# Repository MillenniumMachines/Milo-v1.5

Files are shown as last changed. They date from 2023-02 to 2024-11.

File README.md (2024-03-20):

# Millennium Machines Milo v1.5

<p align="center">
  
</p>

Based on the OpenBuilds MiniMill, the Millennium Machines Milo is an open-source project for DIYers to create a reliable, low cost and powerful desktop CNC mill on their own terms. The mill is designed to have the ability to cut aluminium but is also capable of cutting a vast range of softer materials such as composites, woods and plastics.

To get started we'd recommend going through the [documentation](https://diycnc.xyz/docs) - where you can learn about the parts and work needed to get your own machine up and running.

If you would like to follow the development of Milo, please follow us on Reddit: [r/MilleniumMachines](https://www.reddit.com/r/MilleniumMachines/) or join our [Discord](https://discord.gg/ya4UUj7ax2)

---

## Examples

<p align="center">
  
</p>

<p align="center">
  
  
</p>

<p align="center">
  
</p>

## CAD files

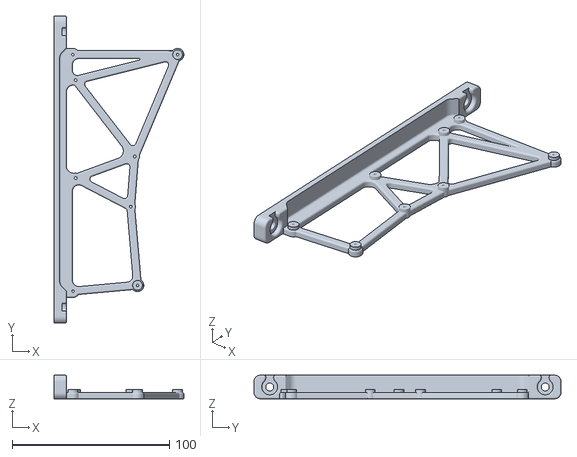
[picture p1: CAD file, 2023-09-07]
STL Files/Electronics Table/Mainboard Mount x1.stl
82.4 x 195.0 x 15.0

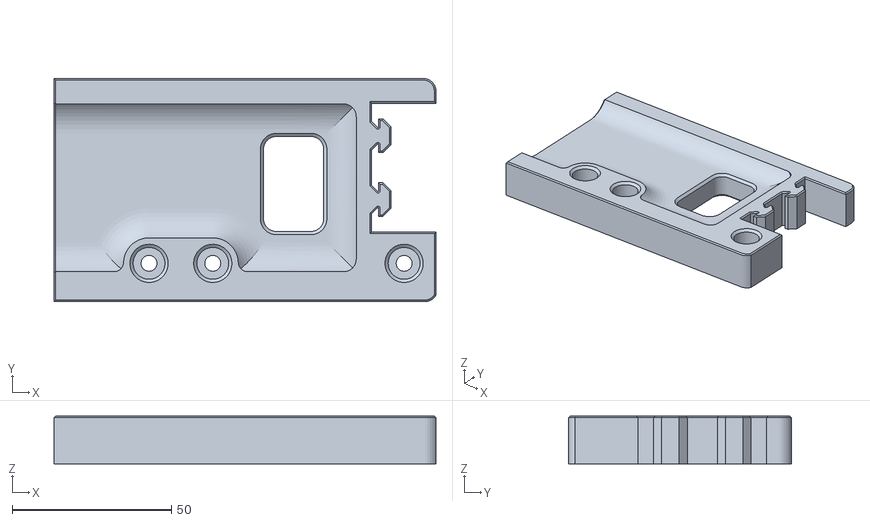
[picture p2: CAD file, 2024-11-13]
STL Files/Electronics Table/Rear Skirt A x1.stl
119.8 x 70.0 x 15.0

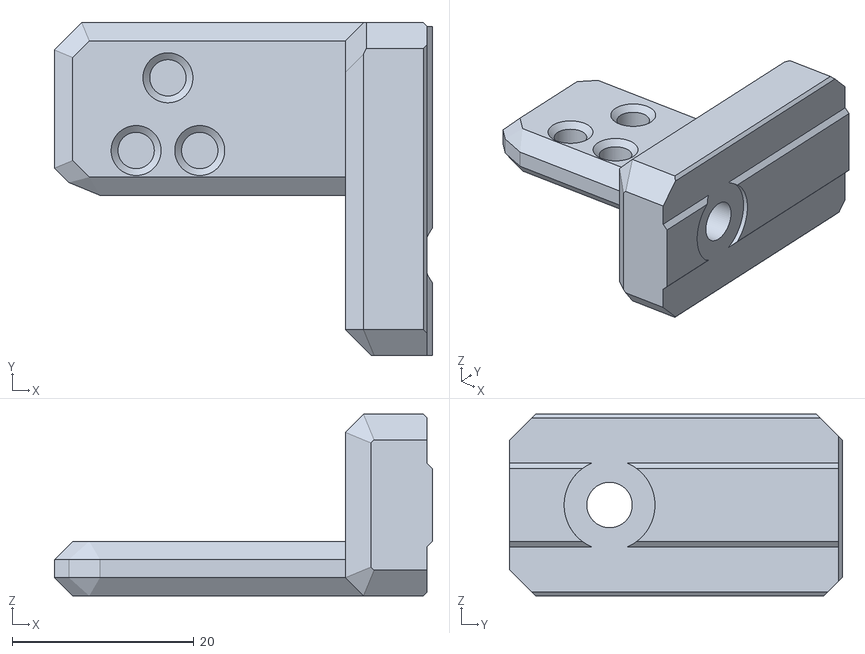
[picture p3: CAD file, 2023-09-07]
STL Files/Minimill Main/Cable Chain Mounts/[a] Z Drag Chain Mount A x1.stl
41.6 x 36.6 x 20.0

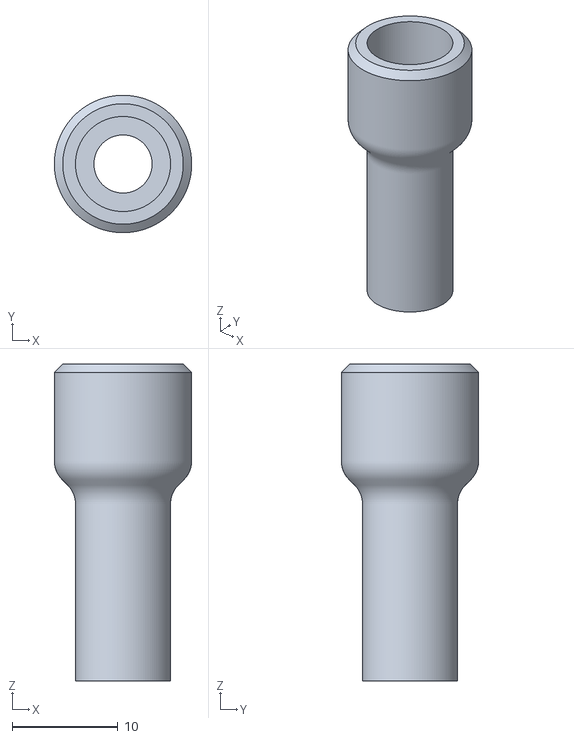
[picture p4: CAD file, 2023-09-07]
STL Files/Minimill Main/Hand Wheels/Handwheel Handle x2.stl
13.0 x 13.0 x 30.0

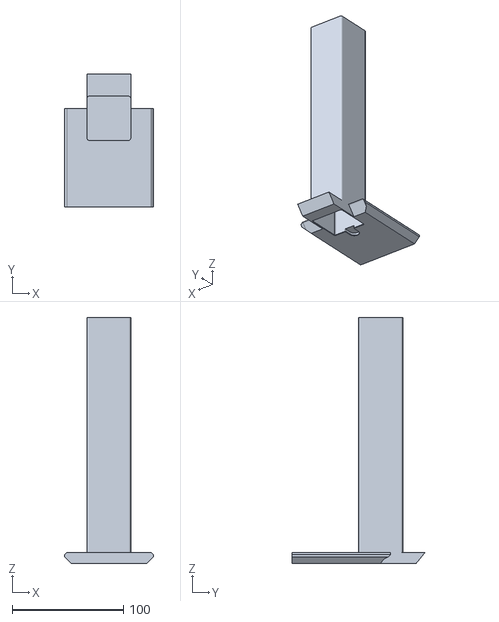
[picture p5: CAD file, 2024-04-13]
STL Files/Minimill Main/Main Column/Ballast Box x1.stl
80.0 x 119.9 x 221.3

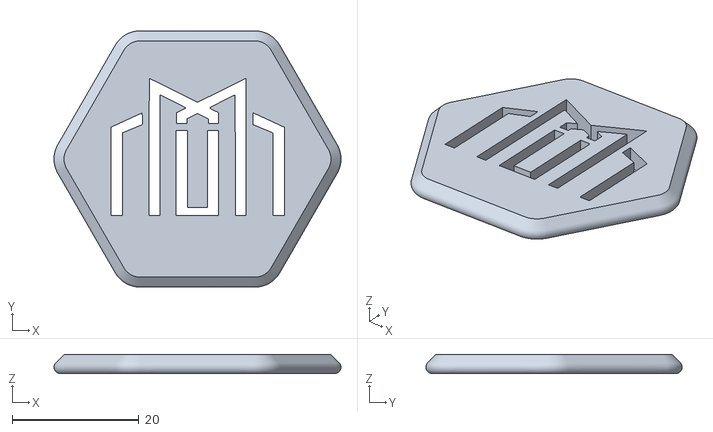
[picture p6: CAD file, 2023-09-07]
STL Files/Minimill Main/Millenium Maker Coin.stl
45.3 x 40.5 x 3.00

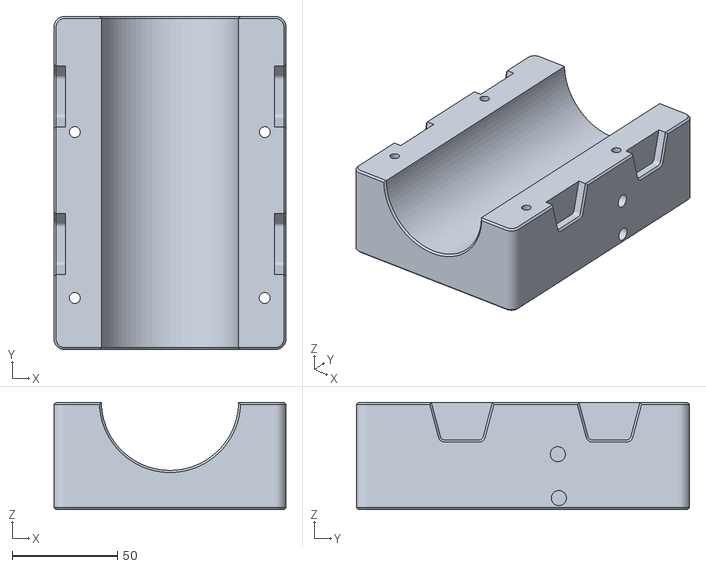
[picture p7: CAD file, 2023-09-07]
STL Files/Minimill Main/Spindle Mount/Spindle Mount 65mm Part B x1.stl
110.0 x 158.0 x 50.9

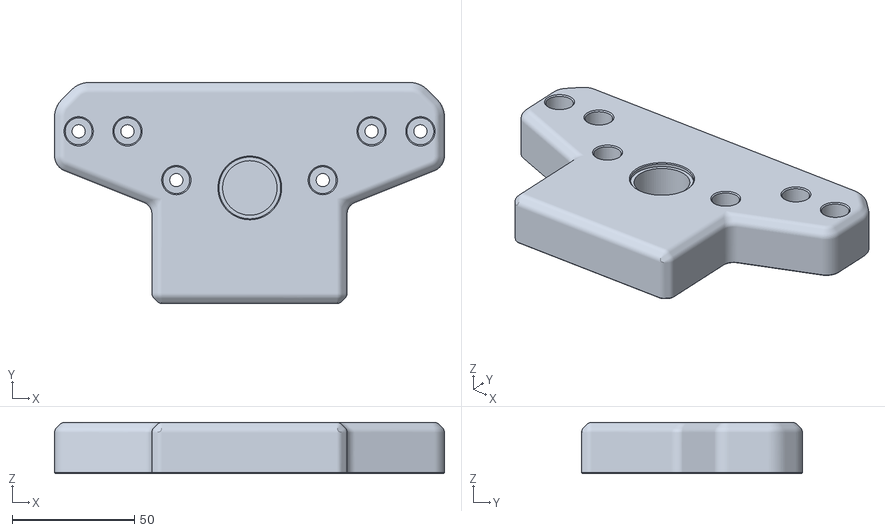
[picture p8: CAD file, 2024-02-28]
STL Files/Minimill Main/X Axis STLs/X Axis Bearing Block x1.stl
159.8 x 90.5 x 21.0

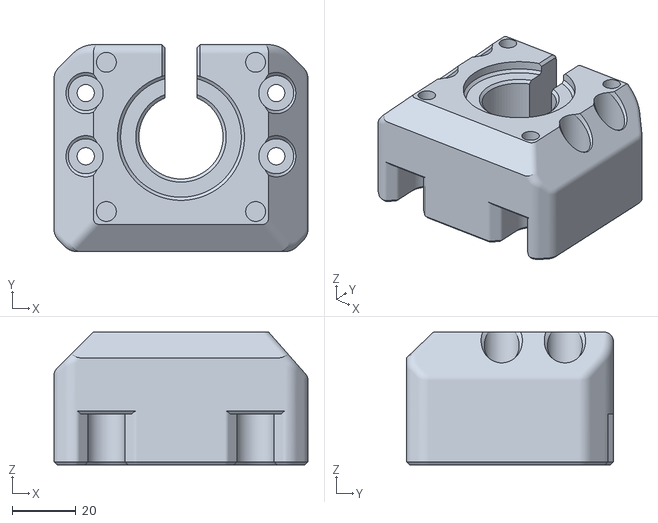
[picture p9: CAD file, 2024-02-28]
STL Files/Minimill Main/Y Axis STLs/Y Axis Motor Mount x1.stl
80.0 x 65.2 x 41.9

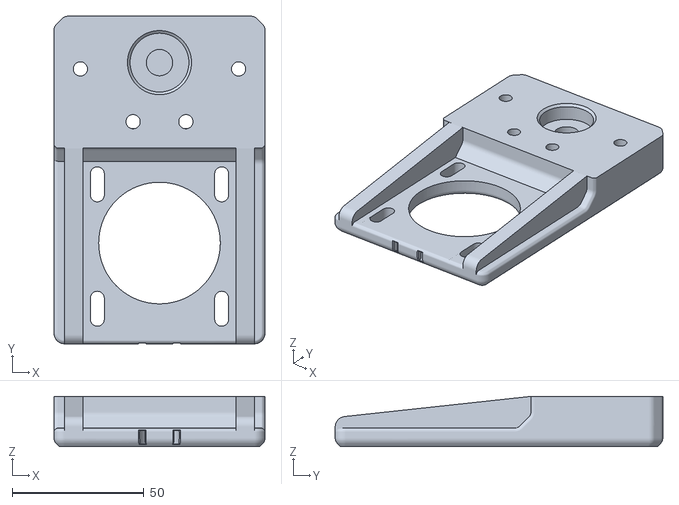
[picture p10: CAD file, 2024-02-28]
STL Files/Minimill Main/Z Axis STLs/Z Motor Mount x1.stl
80.0 x 124.2 x 19.0

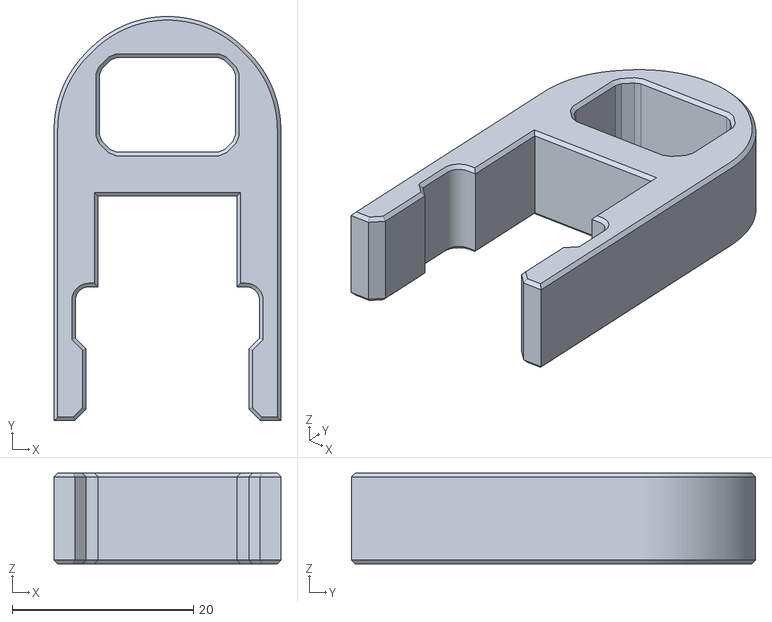
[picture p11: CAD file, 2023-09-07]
STL Files/Tools/Rail Alignment Guide.stl
25.0 x 44.5 x 10.0

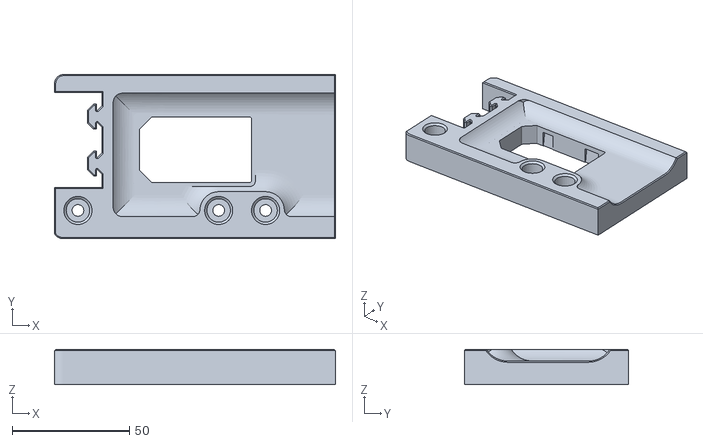
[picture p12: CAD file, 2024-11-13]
STL Files/Electronics Table/Rear Skirt B x1.stl
119.8 x 70.0 x 15.0

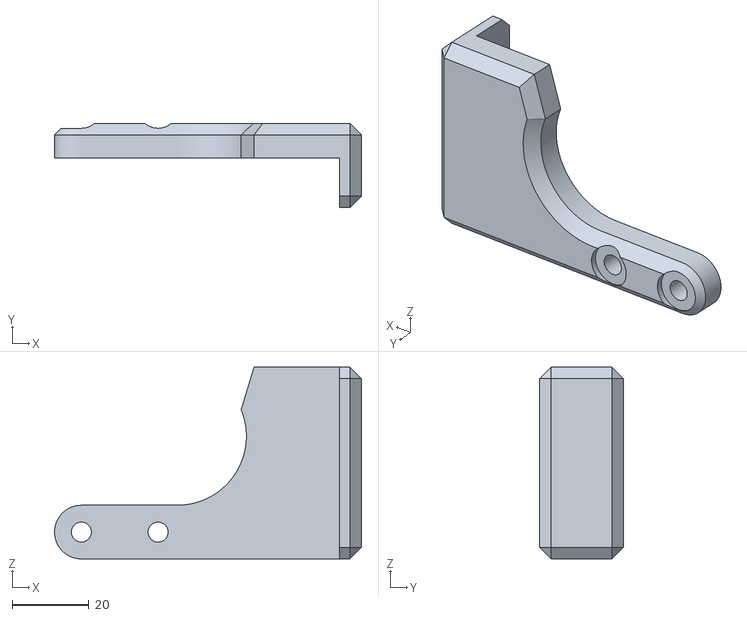
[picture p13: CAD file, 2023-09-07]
STL Files/Minimill Main/Cable Chain Mounts/[a] Z Axis Cable Chain Backer x1.stl
80.0 x 21.9 x 50.0

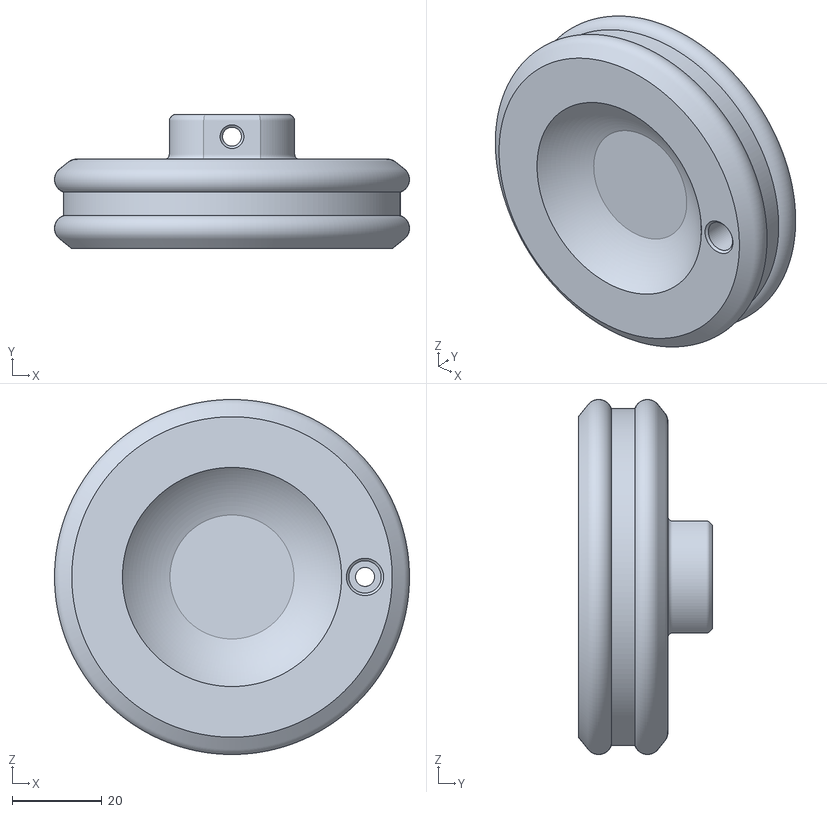
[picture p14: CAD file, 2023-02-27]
STL Files/Minimill Main/Hand Wheels/Handwheel body x2 .stl
79.2 x 30.0 x 79.2

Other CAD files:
STL Files/Minimill Main/Main Column/Column Plate A x1.stl
STL Files/Minimill Main/Spindle Mount/Spindle Mount 80mm Part B x1.stl
STL Files/Minimill Main/X Axis STLs/X Axis Motor Mount x1.stl
STL Files/Minimill Main/Y Axis STLs/XY Plate v1.step
STL Files/Electronics Table/Cable Channel Cover x1.stl
STL Files/Electronics Table/PSU Mounting Bracket A x2.stl
STL Files/Electronics Table/PSU Mounting Bracket B x2.stl
STL Files/Electronics Table/Skirt Front A E-Stop x1.stl
STL Files/Electronics Table/Skirt Front A Hexagons x1.stl
STL Files/Electronics Table/Skirt Front A Solid x1.stl
STL Files/Electronics Table/Skirt Front B E-Stop x1.stl
STL Files/Electronics Table/Skirt Front B Hexagons x1.stl
STL Files/Electronics Table/Skirt Front B Solid x1.stl
STL Files/Electronics Table/TPU Feet x4.stl
STL Files/Electronics Table/[a] Table Bolt Down Bracket A x2.stl
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

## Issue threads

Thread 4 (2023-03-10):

Assembly manual only available through another channel

8000ff, 2023-03-10:
# Currently the assembly manual is available as a google docs

## Documentation not versioned alongside the rest of the project

This creates a high potential for a disconnect between what's written and what's true.
It also prevents people from quickly contributing small changes.

## Documentation format

If the assembly manual is going to be added to this repository, I assume  (maybe, wrongly) that it'll be a PDF.
The PDF format (as a binary format) *can* induce very **big diffs** (changes in the raw file) for even tiny changes in the displayed output, these can create conflicts and prevent a smooth collaborative workflow.

## Recommendation

Knowing this project is maintained and used by a lot of non-developers, I can't recommend going with a "tech heavy" solution (for now) as it would bring too little value and create much work for the maintainers.

I think a good compromise could be using simple markdown files in a docs directory.

Closed 2023-11-24.

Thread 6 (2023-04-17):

Electronics manual missing

kaeru666, 2023-04-17:
I noticed the assembly manual states there is a compendium electronics manual but it is not on the github. If it is there is no mention to where

MilleniumMills, 2023-04-17:
Its being trialled as we speak in the meantime you can ask any questions in our discord and we can answer straight away or explain the basic setup to you.

Closed 2023-11-24.

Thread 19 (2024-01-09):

Tool configurations errors in the tool library

Gloopann, 2024-01-09:
-6mm Flat end mill with 17mm flute length is configured as having 12mm flute length
-6mm Chamfer mill is configured as being 10mm in diameter
-6mm Ball end mill is configured as being made of HSS instead of carbide

Closed 2024-02-16.

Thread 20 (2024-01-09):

Ball end mill from starter pack isn't compatible with Aluminum

Gloopann, 2024-01-09:
The ball end mill from the starter pack is TiAlN coated, which can cause aluminum to weld on the end mill. It should be uncoated or swapped to a coating that doesn't contain Al, such as DLC or TiN coated

mdroberts1243, 2024-03-07:
Can confirm that my LDO kit contains all DLC coated mill bits. (S/N 42)

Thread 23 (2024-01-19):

Convert Electronics Manual to Markdown

benagricola, 2024-01-19:
Working on this here: https://github.com/MillenniumMachines/Milo-v1.5/pull/22

barecool, 2024-01-27:
May I suggest adding a step for the wifi connection
Once you logging to the interface update the config to permanently enable wifi on power on / reboot by adding m552 s1 to the config

benagricola, 2024-02-12:
Changed the title to take @barecool request into account - #22 was merged previously.

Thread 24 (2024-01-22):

print list document still references a 65mm spacer - remove

joshmurrah, 2024-01-22:
there's still reference to a 65mm reducer ring in the print list document - I assume this was supplanted by the actual 65mm front/back spindle mount parts, and it needs to be removed.

Closed 2024-02-16.

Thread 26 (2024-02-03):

Add fly wiring pin out into electronics manual

dmason1992, 2024-02-03:
Missing - confusion of where the drivers needed to go could be avoided by including this

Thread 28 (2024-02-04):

Heat set inserts hole sizes and lengths

dmason1992, 2024-02-04:
CNC kitchen recommends a 3.9mm hole which means LDO should either match, or will ideally require modified parts.

The LDO kit included a couple lengths of M3 heatsets but there is only one line item in the BOM, I'm guessing pointing to the longer version?

The pockets in at least some of the printed parts aren't deep enough for the longer version though.

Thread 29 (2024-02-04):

Documentation recommendations

dmason1992, 2024-02-04:
Page 17 – M3x5mm SHCS (12 screws or 16 screws?)
Page 18 – M3 heatset inserts (what size? LDO send two different M3 lengths)
Page 20 – M3 heatset inserts (what size? LDO send two different M3 lengths)
Page 28 – Spacing for Rails? (noted about butting it against the Idler end)
Page 46 – 2080 or 2040?
Page 60 – LDO has different C extrusion lengths? (320,320,25,120)
Page 68 – Missing step for screwing the linear rails

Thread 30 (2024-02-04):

[BUG: DOC] Need more guidance on antibacklash nut asdemnly

dmason1992, 2024-02-04:
**Describe the bug**
Antibacklash nuts require a bit of a knack to get right and current documentation isn't clear enough

**Document Name**
Assembly manual (X, Y and Z axis assembly pages)

**Expected correction**
A clear and concise description of how to install them. Possibly a link to a video that demonstrates the feel of a correctly assembled antibacklash nut

**Screenshots**
If applicable, add screenshots to help explain your problem.

**Additional context**
Add any other context about the problem here.

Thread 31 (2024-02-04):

[BUG: DOC] LDO VFD PWM on neopixel port not bed out

dmason1992, 2024-02-04:
**Describe the bug**
LDO VFD PWM on neopixel port not bed ou

**Document Name**
Electronics manual / firmware installation

**Expected correction**
Add note at wiring stage to make sure to refer to LDO wiring docs if using their breakout board as some things are different.

Add note to firmware stage to apply correct pin usage for VFD

**Screenshots**
If applicable, add screenshots to help explain your problem.

**Additional context**
Add any other context about the problem here.

camerony, 2024-02-04:
[config.zip](https://github.com/MillenniumMachines/Milo-v1.5/files/14158610/config.zip)

Please test

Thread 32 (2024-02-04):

BOM error for M5 T-nuts

jakep82, 2024-02-04:
I'm almost done building a stock (non FMJ) Milo, and found the BOM to be innacurate for M5 T-nuts.  By my count the mill requires 120 to complete, but I could be off by a couple.  The BOM currently calls for 90.

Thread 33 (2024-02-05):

Tool setter needs more clearance for switch to avoid it breaking

dmason1992, 2024-02-05:
**Describe the bug**
Tool setter doesn't have enough clearance for switch which has lead to a few people breaking them

**Part Name / File Name**
Long John tool setter

**Required Resolution**
Add additional clearance to allow easier installation

**Screenshots**
If applicable, add screenshots to help explain your problem.

**Additional context**
Add any other context about the problem here.

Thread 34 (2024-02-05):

[BUG: DOC] Missing infographic on part assembly for Long John Kit

3DMakerNoob, 2024-02-05:
**Describe the bug**
The spring supplied with the LDO Motors Long John kit is missing in the assembly manual image.

**Document Name**
Manual/Long John Toolsetter Assembly manual .pdf

**Expected correction**
Needs visualization on where the spring should be installed

**Screenshots**
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

**Additional context**

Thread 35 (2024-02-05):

[BUG: DOC] Add diagram to clarify connection between XY assembly and table

Charles-W4, 2024-02-05:
**Describe the bug**
It is unclear to me where and how many of the 90 degree corner brackets are placed. I could see 4 pictured at the ends, but apparently there are 6 per discord.

**Document Name**
Table assembly, page 96 of PDF. Not in markdown docs yet.

**Expected correction**
6 brackets and rough locations

**Screenshots**
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

EdwardChamberlain, 2024-02-11:
This image added to the online manual should clarify this!
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

Closed 2024-02-11.

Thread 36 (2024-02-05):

[BUG: DOC] Markdown doc has wrong image in y-axis assembly

Charles-W4, 2024-02-05:
**Describe the bug**
Image of Y axis backlash nut being installed is repeated as image for X

**Document Name**
/docs/assembly_manual/chapters/y_axis_assembly.md
PDF is correct

**Expected correction**
Update to correct image of X axis backlash nut being installed

**Screenshots**
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

Closed 2024-02-06.

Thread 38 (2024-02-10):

[BUG: DOC] Add a clear view of jumper settings(red jumpers on image) on the Fly CDY V3

barecool, 2024-02-10:
**Describe the bug**
Add a clear view of jumper settings(red jumpers on image) on the Fly CDY V3

- TMC2209 Driver Jumper for UART
- CNC/laser jumper
- Z axis jumper

**Document Name**
Wiring Diagram

**Expected correction**
add image similar to the one attached below with the jumpers highlighted
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

**Screenshots**
see above

EdwardChamberlain, 2024-02-16:
Are these jumpers in the image you have shared in the correct place?

Closed 2024-02-17.

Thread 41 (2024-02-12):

[BUG:DOC] Add spindle earthing to Electronics Manual

benagricola, 2024-02-12:
See print nc wiki for info

https://discordapp.com/channels/810620766756012072/1158419436345249822/1197616574790635551

EdwardChamberlain, 2024-02-16:
We currently have a note in the docs about this

https://github.com/MillenniumMachines/Milo-v1.5/blob/8b68b9656a596b9a22c6efe804fb264637a555b9/docs/electronics_manual/chapters/assemble_electronics.md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

But could do with a dedicated image for this.

EdwardChamberlain, 2024-02-16:
There is also a link to the print NC wiki - I think referring to that is as good as copying the info ourselves.

Closed 2024-02-16.

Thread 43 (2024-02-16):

[BUG: DOC] Add example digital VFD wiring

EdwardChamberlain, 2024-02-16:
**Describe the bug**
No current description of the VFD wiring for connection to the control board.

**Part Name / File Name**
https://github.com/MillenniumMachines/Milo-v1.5/blob/f14d5965a3ed6f9a71a23479c601e5e49b449525/docs/electronics_manual/chapters/assemble_electronics.md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

**Required Resolution**
Add a "typical" (LDO kit) wiring for the VFD and spindle.

**Screenshots**
-

**Additional context**
-

Closed 2024-02-16.

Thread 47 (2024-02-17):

Change all bearing hole dia to 22.3 as current fit is a touch loose

dmason1992, 2024-02-17:
**Describe the bug**
bearing fits are all a bit loose.

**Part Name / File Name**
X bearing block
Y bearing block
Z bearing block

**Required Resolution**
Voron guys printing them have suggested 22.2mm dia based on their testing

**Screenshots**
N/A

**Additional context**
N/A

Closed 2024-02-28.

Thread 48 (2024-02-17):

Spindle docs state wrong size inserts

dmason1992, 2024-02-17:
**Describe the bug**
Spindle block instructions state 2 x m3 inserts but it should be 2 x m5

**Document Name**
([Document name and page number](https://millenniummachines.github.io/Milo-v1.5/assembly_manual/chapters/z_axis_assembly/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,Spindle%20Mount,-Components%20Required))

**Expected correction**
Replace  m3 inserts with m5 in bom for this step and in instruction text

**Screenshots**
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

**Additional context**
N/A

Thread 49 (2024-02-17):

Hold down brackets holes for feet too short

8000ff, 2024-02-17:
**Describe the bug**
Holes for the feet in the table hold down brackets are too short for the 10.5mm inserts according to Dave.

**Part Name / File Name**
Table hold down brackets

**Required Resolution**
Lengthen the holes

Ping Dave if more info required.

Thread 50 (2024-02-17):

Have a cutout for the SD card on the motherboard mount

8000ff, 2024-02-17:
**Is your feature request related to a problem? Please describe.**
No cutout in the motherboard mount makes it tricky to get the micro SD card in/out

**Describe the solution you'd like**
[Use the LDO model](https://github.com/MotorDynamicsLab/LDO-Milo-V1.5/blob/master/STLs/Electronics%20Table/Mainboard%20Mount%20x1_LDO.stl)

**Additional context**
Submitted on behalf of Dave during livestream

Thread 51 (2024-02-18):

ABS shrinkage

dmason1992, 2024-02-18:
**Describe the bug**
Lots of parts suffer a bit from ABS shrinkage which can make it hard to align the printed holes with the extrusion tapped holes. We have avoided the issue by drilling out the holes a bit which normally gives the extra 0.1 to 0.2mm clearance needed for the bolts to work

**Part Name / File Name**
All printed parts that interface with extrusion threaded ends

**Required Resolution**
Suggest a small % scaling to part when printing? or add some more clearance by default to hole sizes

**Screenshots**
See steve builds stream - https://www.youtube.com/watch?v=86LGVIrC2XQ
2:40 ish

**Additional context**
N/A

EdwardChamberlain, 2024-02-23:
We can also roll in the counterbore bridging into this change to remove the need for post processing.

Closed 2024-02-28.

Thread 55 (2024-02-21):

Errant hole in ballast box

EdwardChamberlain, 2024-02-21:
**Describe the bug**
There is an additional hole in the ballast box which is no longer required.

**Part Name / File Name**
Ballast box.stl

**Required Resolution**
remove hidden hole

**Screenshots**
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

**Additional context**
Add any other context about the problem here.
N/A

Closed 2024-02-28.

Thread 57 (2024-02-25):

M5x8 bolts on underside of table brackets are a bit short

dmason1992, 2024-02-25:
**Describe the bug**
M5x8 bolts on underside of table brackets are a bit short which means they barely engage in the t nuts

**Part Name / File Name**
X table brackets

**Required Resolution**
to avoid BOM changes suggest counterbore depth increased by 2mm to allow more threads to engage

**Screenshots**
If applicable, add screenshots to help explain your problem.

**Additional context**
Add any other context about the problem here.

yomgui1, 2024-07-11:
I've also noticed that.
On LDO parts they have added a countersink, not a counterbore. But it may not work. I've good printed pieces with perfect size tolerance and surface finish, my sourced screws have a flat surface, but even with that it's barely enough to engage the screw and have few threads.

I've also tested the M5x10 on original parts: may also not be a good solution for some people due to final tolerances: it works for me, but only a space of 0.2mm remains between the tip of the screw and the extrusion at a good tighten. That's too small.

I'm agree with you on adding a counterbore (than a countersink) is a good compromise to keep the BOM. But it may also decrease the strength of the parts... and these are structural parts.
So, I think 1mm of counterbor is enough to keep enough plastic and strength.

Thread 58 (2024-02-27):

TPU feet hole for insert size is too big

dmason1992, 2024-02-27:
**Describe the bug**
TPU feet hole for inserts is too big and they are loose

**Part Name / File Name**
TPU feet

**Required Resolution**
Reduce hole size (at least inline with other parts. possibly smaller due to flexy nature of TPU)

**Screenshots**
see stream at 54 minutes

(https://www.youtube.com/live/WmmRMIzL28I?si=z1HBU6jeW8mAj3Mf)

**Additional context**
Add any other context about the problem here.

ShaneDelmore, 2024-03-23:
[Milo_Foot_FIXED.stl.zip](https://github.com/MillenniumMachines/Milo-v1.5/files/14730388/Milo_Foot_FIXED.stl.zip)

Here is a fix, I tested it and the sizing was correct for me.  I am just uploading this, the fix was created by West3d.com.

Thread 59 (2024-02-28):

Bootstrapping in aluminum

tkircher, 2024-02-28:
Are there any plans to design parts for a more capable mill made from aluminum parts that can be machined on this mill? It's definitely possible for a conventional mill made from aluminum to machine steel.

EdwardChamberlain, 2024-02-28:
A lot of the parts on v1.5 could be adapted to be made from aluminium with minor modifications! currently we already recommend aluminium XY plates, FMJ, 'FIXATED' aluminium table and 'hearts of iron' metal spindle mounts.  It is on our radar and hopefully we can bring more bootstrap components to milo soon.

tkircher, 2024-02-28:
The design requirements for 3D printing and for machining in aluminum are extremely different, given that aluminum parts don't have the anisotropy or material weaknesses of printed parts, but are also more limited to conventional machining steps. So a machine intended to be machined on this machine would have to be designed from scratch with that in mind, and would have a more conventional small-scale mill design, like dovetails and a saddle.

Closed 2024-02-28.

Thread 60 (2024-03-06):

Single piece skirts

dmason1992, 2024-03-06:
**Is your feature request related to a problem? Please describe.**
Single piece skirt would be stronger for the table than the two piece one.

**Describe the solution you'd like**
Add option of single piece skirt for those with large enough printers.

**Describe alternatives you've considered**
Some form of mechanical joint between the two half width skirts to add the same support

**Additional context**
N/A

stvptrsn, 2024-03-08:
Corrected the heatset depth holes for the M5 inserts that go in the bolt down brackets to fit the LDO supplied inserts.
Changed from sacrificial bridges to "cross bridge" on the bolt down bracket M5 bolt holes.
Cleaned up some fillets on the rear skirt.
Combined front and rear skirts into one piece each.
[Milo_Skirts_1piece.zip](https://github.com/MillenniumMachines/Milo-v1.5/files/14532987/Milo_Skirts_1piece.zip)

stvptrsn, 2024-03-13:
Adding LDO modified one piece rear skirt.  Corrected power inlet tab locations.
[Rear_Skirt_LDO_1pc.zip](https://github.com/MillenniumMachines/Milo-v1.5/files/14594831/Rear_Skirt_LDO_1pc.zip)

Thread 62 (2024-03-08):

M3 heat set inserts are tight and  can melt through wall

EdwardChamberlain, 2024-03-08:
**Describe the bug**
Inserting the M3 heat set inserts in not the anti backlash nuts can cause the plastic to melt and block the space where the nut needs to go

**Part Name / File Name**
X, Y, Z anti backlash nuts

**Required Resolution**
Open holes to reduce plastic movement

**Screenshots**
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

**Additional context**
Add any other context about the problem here.

mo22de, 2024-08-13:
I dont think you can make the M3 holes any bigger, and also you cant move them outwartds, because the backlash nuts have the holes like it is. If you reallly want to make this a better design, and i think that would make sence, cause ths is really not an optimal soution, we need other backlash nuts with a wider outer ring, or maybe a rectangular design, so the M3 holes can move outwards more.

I got only one wall line between the lead-screw hole and the heat-insert hole, printing it the same orientation like the picture shows. That didnt work out well. Walls were not even printed really bulding a wall.
So, I printed it again oriented with the lead srew hole showing up. The print turns out better and the wall between the holes is much better.

Still while pushing in the M3 heat-inserts, the inner hole can deform a little. I got it fitting by heating both heat inserts up, to temperature and than push in the lead screw nuts while ASA is still hot.

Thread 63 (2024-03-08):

Lead screw nut holes slightly too tight.

EdwardChamberlain, 2024-03-08:
**Describe the bug**
Inserting the lead screw nuts requires a small amount of force.

**Part Name / File Name**
X, Y, Z anti backlash nuts

**Required Resolution**
Open hope by a fraction

**Screenshots**
If applicable, add screenshots to help explain your problem.

**Additional context**
Add any other context about the problem here.

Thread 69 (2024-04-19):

Please add the full CAD to the repository.

benvanik, 2024-04-19:
The upstream repository has a CAD/ directory with a step of the full Milo. When planning mods based on the LDO Milo it'd be very useful to have a common model builders can use with the adjusted LDO parts and sizing from the FMJ height increase.

The readme has a screenshot of the CAD - can whoever has that please add it to the repository?

benvanik, 2024-04-20:
(whoops, I put this in the wrong repository *facepalm* this was meant for the LDO repo)

Closed 2024-04-20.

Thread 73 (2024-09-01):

Rear Skirt Counterbores wrong depth

MrSniperPhil, 2024-09-01:
As described by Hazzert in discord bug-report channel, the rear skirts have a shallow counterbore which leads to only 2mm thread engagement with the M5x12 screws.

**Part Name / File Name**
STL Files/Electronics Table/Rear Skirt A x1.stl
STL Files/Electronics Table/Rear Skirt B x1.stl

**Required Resolution**
Deepen the counterbores by 3mm to make them equal to the front counterbores.

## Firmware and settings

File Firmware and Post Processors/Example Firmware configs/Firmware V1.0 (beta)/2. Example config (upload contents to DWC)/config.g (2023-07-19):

;FIRMWARE NAME :            Millennium Milo V1.5 (STOCK)
;FIRMWARE VERSION :         RRF 3.4
;FIRMWARE CONFIG VERSION :  VERSION (BETA) v1.0
;CONTROL BOARD :            Mellow Fly CDY V3 

;This firmware has been modified by the Millennium Machines team to be used as an example config alongside a Mellow Fly CDY V3 control board
;and contains common pin maps for this board.

;===========================================================================
;============================= Getting Started =============================
;===========================================================================

;Here are some useful links that may help you get your mill setup

;DUET G-CODE DICTIONARY :                  https://docs.duet3d.com/en/User_manual/Reference/Gcodes

;PRUSA CALCULATOR FOR E-STEPS AND ACCELS : https://blog.prusa3d.com/calculator_3416/

;INSTALLING RRF ON MELLOW FLY :            https://www.youtube.com/watch?v=nhE0Txse3ZQ

;FLY E3 GENERAL INFO BY TEAMGLOOMY         https://teamgloomy.github.io/fly_cdyv3_general.html

;===========================================================================
;============================= Board Specifics =============================
;===========================================================================


;SECTION NAME / G-CODE EXPRESSION              ;DESCRIPTION                                                                               ;DEFAULT VALUES                                


; GENERAL PREFERENCES
G90                                            ; send absolute coordinates...
M550 P"Milo V1.5"                              ; set printer name
M453                                           ; set firmware to CNC Mode


; CONFIGURE NETWORK

M552 S1                                        ; enable network
M586 P0 S1                                     ; enable HTTP
M586 P1 S1                                     ; disable FTP
M586 P2 S1                                     ; disable Telnet


; CONFIGURE DRIVES

;NOTE: To change motor direction in firmware change S=0 to S=1 or vice versa

M569 P0 S0                                     ; physical drive 0 goes forwards using default driver timings                                                                             
M569 P1 S0                                     ; physical drive 1 goes forwards using default driver timings                                                                             
M569 P2 S0                                     ; physical drive 2 goes forwards using default driver timings                                                                             
M569 P3 S0                                     ; physical drive 3 goes forwards using default driver timings                                                                             
M584 X0 Y1 Z2                                  ; set drive mapping   


;===========================================================================
;============================== Motion setup ===============================
;===========================================================================
   
                          
; CONFIGURE AXES

M350 X16 Y16 Z16 I1                            ; configure microstepping with interpolation                                               (DEFAULT X16 Y16 Z16)
M92  X400 Y400 Z800.00                         ; set steps per mm                                                                         (DEFAULT X400 Y400 Z800)
M566 X600.00 Y600.00 Z400.00                   ; set maximum instantaneous speed changes (mm/min)                                         (DEFAULT X600 Y600 Z400)
M203 X3000.00 Y3000.00 Z1000.00                ; set maximum speeds (mm/min)                                                              (DEFAULT X3000 Y3000 Z3000)
M201 X800.00 Y800.00 Z400.00                   ; set accelerations (mm/s^2)                                                               (DEFAULT X800 Y800 Z400)
M906 X1200 Y1200 Z1200 I30                     ; set motor currents (mA) and motor idle factor in per cent                                (DEFAULT X1200 Y1200 Z1200 I30 )
M84 S30                                        ; Set idle timeout                                                                         (DEFAULT S30)


; CONFIGURE AXIS LIMITS

M208 X0 Y0 Z0 S1                               ; set axis minima                                                                          (DEFAULT X0 Y0 Z0 S1)
M208 X335 Y208 Z125 S0                         ; set axis maxima                                                                          (DEFAULT X335 Y208 Z125)
;M564 S0                                       ; allow movement outside axis limits                                                       (DEFAULT S0)


; CONFIGURE ENDSTOPS

M574 X1 S1 P"xstop"                            ; configure switch-type (e.g. microswitch) endstop for low end on X via pin xstop          (DEFAULT X1 S1 P"xstop")
M574 Y2 S1 P"ystop"                            ; configure switch-type (e.g. microswitch) endstop for low end on Y via pin ystop          (DEFAULT Y1 S1 P"ystop")
M574 Z2 S1 P"zstop"                            ; configure switch-type (e.g. microswitch) endstop for high end on Z via pin zstop         (DEFAULT Z2 S1 P"zstop")

; CONFIGURE BACKLASH COMPENSATION 

NOTE : backlash compensation is only available in RRF version 3.5 beta 2 so is disabled for this version of the config by default.
Upgrade to version 3.5 beta 2 should you wish to use it

;M425 X0                                        ;Set backlash compensation for the X axis                                                  (DEFAULT X0)
;M425 Y0                                        ;Set backlash compensation for the Y axis                                                  (DEFAULT Y0)
;M425 Z0                                        ;Set backlash compensation for the Z axis                                                  (DEFAULT Z0)


;===========================================================================
;============================= spindle setup ===============================
;===========================================================================


; SPINDLE

M950 R0 C"PB0+PB9" L24000                       ; Create spindle index 01, with PWM pin on heater 1 and 24000 RPM achieved at full PWM     (DEFAULT R0 C"e0heat" L24000)

; TOOL SETUP

M563 P1 S"Spindle 1" R0                        ; define tool 1 with spindle 01 
G10 P1 X0 Y0 Z0                                ; set tool 1 axis offsets


;===========================================================================
;=============================== CNC OUTPUTS ===============================
;===========================================================================


; CNC OUTPUTS

; Create custom outputs for external features such coolant sprayers, tool changers or relays you may also need to add io pins to ENABLE your spindle (Your imagination is the only limit).
; NOTE : PINS MUST BE ASSIGNED AND OUTPUTS MUST BE UNCOMMENTED BEFORE THESE FEATURES WILL WORK.

;M950 P1 C"XXXX"                               ; create io 1 on pin XXXX (TOOL CHANGER) 
;M950 P2 C"XXXX"                               ; create io 2 on pin XXXX (COOLANT)
;M950 P3 C"XXXX"                               ; create io 3 on pin XXXX (SPINDLE ENABLE) 
;M950 P4 C"XXXX"                               ; create io 4 on pin XXXX (SPINDLE DIRECTION)


;===========================================================================
;====================== MISCELLANEOUS STARTUP SETTINGS =====================
;===========================================================================
 

; Other Settings

;M575 P1 S0 B57600                             ; uncomment to enable support for Mellow fly 4.3/7.0 in touch screen 
M140 H-1								       ; Disable heated bed
M564 S1 H1 								       ; Disable jog commands when not homed
M911 S21.0 R23 P"G91 G1 Z3 F1000" 		       ; Configure power loss resume
M501									       ; Load Stored Parameters 


; initial setup

M5                                             ; STOP SPINDLE
;G28			          					   ; Home all axes on firmware startup (uncomment to enable this function)

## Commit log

2022-11-24 Updated CAD
2022-11-30 fixed hole sizing for heatset inserts
    [X Axis Motor Mount x1.stl, Y Axis Motor Mount x1.stl]
2022-11-30 Modified depth of counterbores to better fit M5x12 BHCS
    [Skirt front A E-Stop x1.stl, Skirt front A hexagons x1.stl, Skirt front A solid x1.stl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]
2023-01-29 updated kit sourcing list
    [Milo V1.5 sourcing guide .xlsx, Milo V1.5 sourcing guide.xlsx]
2023-02-17 Dummy rails added and files restructured to include tools
    [Dummy rail.stl, Rail allignement guide.stl]
2023-02-20 Updated Spindle mount, removed reducer and updated CAD
    We made the spindle mount easier to print and added 2 sizes for 65 and 80mm spindles removing the need for the spindle reducer. The CAD and print list have been updated to reflect these changes.
    [65mm Reducer x1.stl, Milo V1.5 print list.xlsx, SMH 70mm part A x1.stl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]
2023-02-20 updated print list PDF
2023-02-20 updated accent colour tag
    [[a] Spindle mount 65mm part A x1.stl, [a] Spindle mount 80mm part A x1.stl]
2023-02-22 Added TPU feet
    [TPU feet x4.stl]
2023-02-26 Increased depth of heat insert holes
    [X Axis Motor Mount x1.stl]
2023-02-27 Made handwheels easier to print updated CAD
    [Handwheel body x2 .stl]
2023-02-27 fixed issue with 80mm mount chamfers
    [[a] Spindle mount 80mm part A x1.stl]
2023-03-23 Create MINIMILL V1.5 ASSEMBLY MANUAL.pdf
2023-04-01 Updated Anti backlash nuts to fix some issues
    [X Axis Anti Backlash Nut x1.stl, Y Axis Anti Backlash Nut x1.stl, Z Axis Anti Backlash Nut x1.stl]
2023-04-01 Added rail carriage grease packing tool
2023-04-09 updated sourcing guide
    [Milo V1.5 print list.xlsx, Milo V1.5 sourcing guide .xlsx]
2023-04-12 Updated Y axis motor mount and manual
    [Y Axis Motor Mount x1.stl]
2023-05-07 Update CAD.zip
    Fixed issue with unresolved external component
2023-07-19 Added firmware open beta files
    [bed.g, config.g, homeall.g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]
2023-09-04 rotate the STLs in their printing orientation
    [Ballast box x1.stl, Ballast cap x1.stl, Cable channel cover x1.stl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]
2023-09-30 Revert "updates"
    This reverts commit d0d8b2cf75d96637222401c1dd9d797e39b4b22f.
    [bed.g, config.g, homeall.g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]
2023-09-30 Revert "updates"
    This reverts commit 38b2b8bc7713a257d3bb8b64fbefd807eb98d087.
    [Millenium Maker Coin.stl]
2023-09-30 Revert "rotate the STLs in their printing orientation"
    This reverts commit e576c7913e62531bb1e293d08b3cd0cd4a60a340.
    [Ballast box x1.stl, Ballast cap x1.stl, Cable channel cover x1.stl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]
2023-09-30 Revert "Revert "rotate the STLs in their printing orientation""
    This reverts commit db31b9440b19355abe2d3d405459e1e9e28ec801.
    [Ballast box x1.stl, Ballast cap x1.stl, Cable channel cover x1.stl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]
2023-09-30 updating firmware
    [bed.g, config.g, homeall.g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]
2023-11-05 Update Y Axis Motor Mount x1.stl
2023-11-21 Restructure file layout for consistency
    - Remove extraneous spaces and file extensions
    - Rename STL files consistently
    - Move zips of CAD files into subdir
    - Rename misspelled `ressources` folder
    - Update references to renamed files in Markdown docs
    [Ballast Box x1.stl, Ballast Cap x1.stl, Ballast box x1.stl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]
2023-11-21 Grammar and formatting changes
    Various changes to make the assembly manual a bit more consistent.
    - Capitalisation changes to match new STL filenames.
    - Capitalisation changes to headers and subsections.
    - Grammar changes to ease readability.
    - Formatting changes for notes.
    - Replace "Loctite" (brand name) with "medium-strength thread-lock"
    where relevant. We don't want people putting permanent
    thread-lock on stuff because it said "Loctite" on it 😅
    - Move CAD zip files into a subdirectory.
2023-11-21 Update markdown BOM with new spindle
2023-11-21 Fix capitalisation in markdown BOM
    Fix some more syntax / spelling issues in the sourcing guide.
2023-11-22 And missing Y axis step and fix backgrounds
2023-11-24 Fix broken BOM link and remove extraneous readme
    The BOM link was a 404 and the docs readme.md file has been replaced
    with index.md which is more appropriate for switching to automated docs
    generation.
2023-12-07 Rename links to organisation / repos
    - Self-referential links are updated to MillenniumMachines organisation
2023-12-07 Make STL links absolute to github
2023-12-07 Set custom accent colours for material
2023-12-07 Add fade to images
    Also rework Z-Axis assembly page with new styling that adds additional
    clarity, calls out components required for each major step and calls out
    important warnings and notes.
2023-12-07 Add printable annotations
2023-12-07 Split sourcing tables, revert assembly images
2023-12-07 Y-Axis rewrite in progress
2023-12-07 Further work on X-Axis assembly
2023-12-07 Finish XYZ assembly pages
    - Add missing y-axis step 90.1
    - Rename Z-Axis bearing block for consistency
    - Various improvements to intro and hardware reference
    - Add stub electronics manual
    - Add basic FAQ
    [[a] Z Axis Bearing Block x1.stl]
2023-12-07 Add filament question
2023-12-07 Add missing table assembly step
2023-12-07 Various documentation changes
    - Reorder hardware reference
    - Small clarify and syntax changes to assembly manual introduction
    - Various FAQ updates and clarifications
    - Call out layer-height requirement in printing guide
    - Update accent Y/N format and quantity alignment
2023-12-07 Combine XY and Z gantry plate warnings
    Slight tweak to printing guide
2023-12-08 Clean up FAQ questions and headings
    Additionally fix syntax error in assembly intro and replace elipses with
    periods.
2023-12-16 Combine X and Y leadscrew lines in bom
    Some confusion around why there is 'duplicate' lines for the X and Y
    lead-screws.
    This combines them both into a single line with quantity 2, highlighting
    that they are used for the X and Y axes.
2023-12-19 Add FMJ assembly steps
2023-12-19 Add finalised FMJ bolt count
2023-12-29 Update Y motor mount image
    Also update assembly instructions.
2024-01-08 Update MILO V1.5 ASSEMBLY MANUAL.pdf
2024-01-08 Set orientation of new Y axis motor mount
    [Y Axis Motor Mount x1.stl]
2024-01-09 Assembly manual Z- and Y-Axis fixes
    - Remove extraneous annotations on X and Y Anti-Backlash nut assembly
    instructions.
    - Fix repeated drag-chain image.
    - Fix STL link to Z-Axis bearing block.
2024-01-09 Revert PDF assembly manual rename
2024-01-10 Move rail and loctite warnings before assembly
2024-01-15 Update various old Y motor mount images, add FMJ bolt note
2024-02-05 Add files via upload
    This plate is ment to be milled, if you decide to 3d print it, make sure it is as strong as you can make it. This is a Priority #1 upgrade part if you start off with a printed piece.
    [Z plate.stl, Z-mounting-plate.step]
2024-02-05 This plate is ment to be milled, if you decide to 3d print it, make sure it is as strong as you can make it. This is a Priority #1 upgrade part if you start off with a printed piece.
    [XY Plate v1.step, XY_table_plate_v2.stl]
2024-02-05 Update y_axis_assembly.md
    fixes #36
2024-02-09 Update MINIMILL V1.5 ASSEMBLY MANUAL.pdf
2024-02-11 added y axis motor mount change
2024-02-11 added LDO insert length note
2024-02-11 Added foot assembly stage
2024-02-11 added final step of table assembly
2024-02-13 More compact vfd wiring
2024-02-16 Update Milo V1.5 Print List.pdf
    Removed 65mm Reducer from Print List
    Corrected Front Skirt B being listed as Rear Skirt B
    Fixes Issue #24
2024-02-16 added vfd wiring (digital) exmaple for SL3
2024-02-20 Flip Y-Axis Step 51 image
2024-02-28 Enlarged holes to 5.4 mm + counterbore bridging + Bearing Bore Adjustment (#56)
    * Enlarged holes to 5.4 mm + counterbore bridging
    * adjusted bearing bore to 22.3
    * removed hole in ballast box fixes #55
    [Ballast Box x1.stl, X Axis Bearing Block x1.stl, X Axis Motor Mount x1.stl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]
2024-03-20 Remove firmware config, old docs and workflow (#64)
    Firmware configuration is now moved to
    https://github.com/MillenniumMachines/RRF-Configs and documentation has
    been moved to https://millenniummachines.github.io/docs - which means we
    don't need any workflow steps in this repo anymore.
    We also move the Post-Processor into its own top level folder as it no
    longer has a firmware folder as sibling.
    [bed.g, config.g, homeall.g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]
2024-04-13 feat: ballast flip (#68)
    [Ballast Box x1.stl]
2024-04-29 Fix-up filename (#66)
    [[a] Z Axis Cable Chain Backer x1.stl]
2024-07-14 Added Bottom Plate DXF (#71)
    As raised in Issue #70, the Bottom Plate DXF was missing from all the files.
    [bottom_plate.dxf]
2024-11-13 Corrected counterbore depth on Rear Skirts (#74)
    * Added Bottom Plate DXF
    * Corrected counterbores for depth
    * fix: remove duplicate file and orient
    ---------
    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
    [Rear Skirt A x1.stl, Rear Skirt B x1.stl]
